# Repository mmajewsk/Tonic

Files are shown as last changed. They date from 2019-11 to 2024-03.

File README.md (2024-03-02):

<div align="center">
  
# An open-sourced project of autonomous car 
  
[Introduction](#introduction) • [Documentation](#ok-so-how-do-i-start) • [Screenshots] • [Contribute](#contribute) 
  
Tonic logo



[][Discord]

demo

⚠️ ➡️ [Video here](https://www.youtube.com/watch?v=u7oDqWJhXR0) ⬅️ ⚠️

_a.k.a.: "Roomba, that does not suck"_

Written in Python 🐍 (mostly).

</div>

---

### Contents:

- [Introduction](#introduction)
- [Features](#features) 
- [How does it work](#how-does-it-work) 
- [How to start](#ok-so-how-do-i-start)
- [Contribution](#contribute)
- [Related repos](#related-repos)

# Introduction

This repository contains main software and documentation for the Tonic project. This project aims to create an open-sourced autonomous driving system, along with its hardware prototype implementation. Some essential parts of the projects are contained in other related repos. See [the list of related repos](#related-repos)
The core idea of how this should work is as follows:

1. After setting up the robot/car, drive it manually, and dump the video and steering feed (this part is called _data taking_).
2. Create a 3D mapping of the environment with [Tonic/autonomous].
3. Define checkpoints, through which the machine will drive.
4. Program the car to drive on the defined paths.

All of that to be possible for as cheap as possible, with a raspberry PI and only a single camera.

# Features

  

  - Camera live feed and recording.
  - Live steering system and recording.
  - Working IMU live streaming and recording.
  - Working odometry live streaming and recording.
  - Qt GUI client for driving and data taking.
  - SLAM mapping, and navigation implemented with ORB_SLAM2 and its custom fork, custom python bindings, and serialisation.

# How does it work

As for now, this repository ([mmajewsk/Tonic]) contains guides and software for building, running and steering the car 🚘 for the _data taking_.
The code is divided, into [Tonic/control] and [Tonic/car]. 

The [Tonic/control] contains the code that is meant to be run on your laptop/pc/mac, that will control the raspberry pi [Tonic/car].

The machine and control interface is communicating via WiFi network, using sockets. 

Sensors, camera, and steering - each one is implemented as a separate service using sockets.
You can steer it with the keyboard on PC, while seeing live feed from the camera.
All of the sensors, steering and video can be dumped to files on PC.
You don't need to turn all of the sensors to make this work.

**The odometry and IMU are not necessary to make an environment mapping**

# Ok so how do I start

0. Take a look at previous versions and the current one in [video and screenshots][Screenshots].
1. First start by [assembling the hardware](doc/hardware_guide.md).
2. Then set up the [machine and interface software](doc/running_software.md).
3. Do the data-taking run, running steering and video data, [as described here](doc/running_software.md##running-tonic).

To make your machine drive autonomously, follow the guide in [Tonic/autonomous] repo.

# Contribute

🧑‍🔧 This project is meant to be open for everyone. The contributions are welcome.
If you would like to help see what's listed in the issues [here](https://github.com/mmajewsk/Tonic/issues), or add something yourself.

Also, you can join the 🗣️ [discord server][discord] if you are looking for quick help, or just want to say hi ;) 

# Related repos
- [My fork of ORB_SLAM2](https://github.com/mmajewsk/ORB_SLAM2)
- [My fork of Osmap] - Dumps ORB_SLAM2 to file
- [My fork of PythonBindings] - this one combines osmap with orb slam python bindings!
- [TonicSlamDunk] - Install scripts for all of the above, includes scripts for ubuntu, and dockerfile.
- ~~[TonicOrange] - **Exemplary use of orb slam, for pathfinding**~~ (moved to [Tonic/autonomous])

[discord]: https://discord.gg/shmRajSkDz
[mmajewsk/Tonic]: https://github.com/mmajewsk/Tonic
[Tonic/control]: control
[Tonic/car]: car
[My fork of ORB_SLAM2]: https://github.com/mmajewsk/ORB_SLAM2
[My fork of Osmap]: https://github.com/mmajewsk/osmap 
[My fork of PythonBindings]: https://github.com/mmajewsk/ORB_SLAM2-PythonBindings 
[TonicSlamDunk]: https://github.com/mmajewsk/TonicSlamDunk 
[TonicOrange]: https://github.com/mmajewsk/TonicOrange 
[Screenshots]: doc/video_and_screenshots.md
[Tonic/autonomous]: autonomous

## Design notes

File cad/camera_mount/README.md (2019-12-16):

# Description

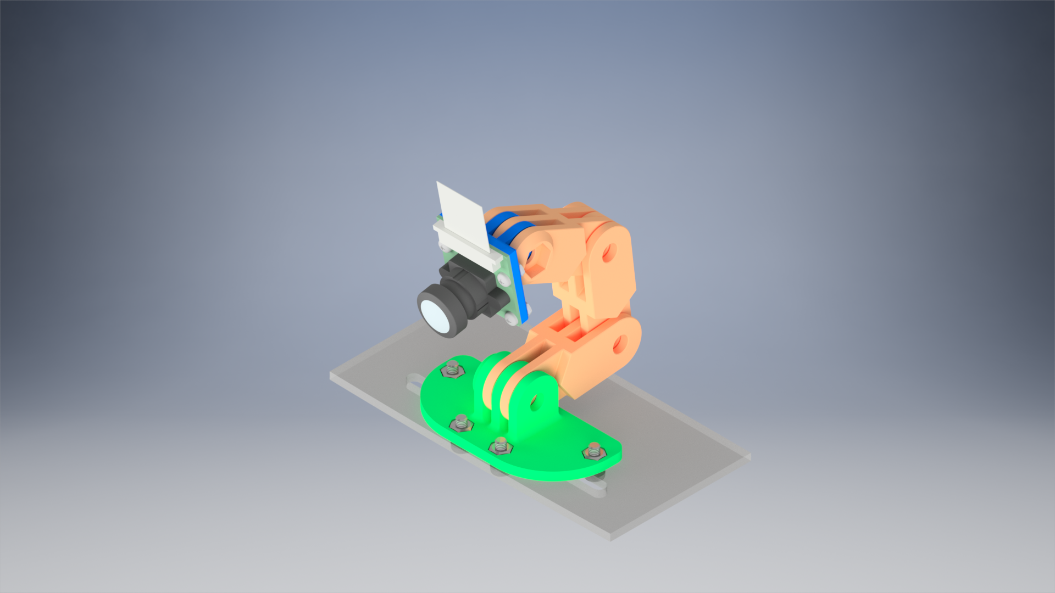
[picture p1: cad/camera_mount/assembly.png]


This Raspberry Pi camera mount makes use of the action cam style bracket connector (aka GoPro-inspired).
IMU mount suits [MinIMU-9 v5](https://www.pololu.com/product/2738).

arm-30-straight-v5-1.stl was borrowed from [https://www.thingiverse.com/thing:2194278](https://www.thingiverse.com/thing:2194278)

Made with Autodesk Inventor 2020

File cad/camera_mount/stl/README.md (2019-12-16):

# Print settings:

The higher infill density you pick the sturdier your parts are going to be.
Go for 100% if you can.

## camera_mount.stl

* Generate supports: yes

## camera_mount.stl

* Generate supports: no

## platform_mount.stl

* Generate supports: yes

## arm-30-straight-v5-1.stl

* Print 3 pieces
* Generate supports: no

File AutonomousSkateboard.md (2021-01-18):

# AutonomousSkateboard

This repository will contain notes on the autnomous skateboard.

# Motivation 

It's cheap. It can move a person around. Can be upgraded to auotonomy. What else do you need? 

# Simmilar work

Hacksmith did a remotely controlled board like that (timestamp points to specific) so I know it's possible, but they dida that with 4 motors.
https://www.youtube.com/watch?v=1g5nzRINaPQ&t=368s
Question is will 2 motors be enough to turn the board around?

# Hardware

If you are not familliar with DIY e-skateboards i suggest watching some videos on this topic [like this one  ](https://www.youtube.com/watch?v=LJqyWRSqOy4).

There are multiple parts availible online to buy and assemble, but the cheapest option is to recycle.
I bought [Nillox Longboard](https://www.nilox.com/es/datasheet/electric-skateboard-30nxskmolo001) for mere ~100€.
It was described as broken, but the description suggested tha the battery and wheels are ok, so I risked buying it.

The battery is 4,4 Ah 36V 10s2p with BMS (Battery Management System) built-in.
The motors are 90mm motors (kind of like [these](https://www.amazon.com/PROMOTOR-Motors-Electronic-Skateboard-Longboard/dp/B07F2Y22Q9?th=1)). I don'thave much details but will work this out.

The internal electronic was kind of fine (the problem with the board not working was only with the remote control itself), but still for better control I needed an ESC (electric speed control).

This is where the wonderful, glorious [VESC](https://vesc-project.com/) project comes in.
TL; DR; its highly customisable, open-source elecetric speed control.
I bought 2x flipsky's version of [VESC](https://flipsky.net/products/torque-esc-vesc-%C2%AE-bldc-electronic-speed-controller) (2x one per motor).

# Controlling the speed

The two VESCs can be connected together to duplicate the steering signal.
The VESC can be connected to mobile app or PC via bluetooth (using a proprietary [bluetooth module](https://flipsky.net/products/core51822-ble4-0-bluetooth-2-4g-wireless-module-nrf51822-onboard-ws82013)]. So that's a nice wireless connection.
The main problem is that VESC was not designed with differential steering (we need to move one wheel faster then the other to make it turn) in mind.
There are two possible sollutions:
 - Use external connection to controll VESCs with PWM (pulse-width modulation), so something like arduino would work
 - Dig into the VESC code to find if it's possible to send a different command to the connected vesc than just to repeat. And modify the code to do so.
 So far I'm opting for the second one since it should be more elegant and versatile, but the first one is far easier to implement, but needs additional hardware.

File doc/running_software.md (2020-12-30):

# Software Guide

So in order to make the robot work, you need to setup everything on raspberry ([car setup](#car-setup)) and on your pc ([remote control](#remote-control)).

## Steps to run in data taking mode

There is some set up required, before you can run this:

0. Set up the [RPI0](#car-setup)
1. (callibrate the IMU, but only if you need it)
2. Set up the `settings.yml` correctly
3. Set up desired services on the RPI0(Video, Steering, Imu, Odometry).
4. [Set up remote control](#remote-control-setup) and run it.

## (Deprecated) Steps to run in live orb_slam mode

There is some set up required, before you can run this:

0. Set up the [RPI0](#car-setup) and [SLAM docker](https://github.com/mmajewsk/orb_slam_py2_docker)
1. callibrate the camera
2. callibrate the IMU
3. Set up the `settings.yml` correctly
4. Set up desired services on the RPI0(Video, Steering, Imu, Odometry), or on laptop (SLAM).
5. Run Tonic 

# Remote Control

## Prerequisistes

**Python** - Of course, Tonic is written almost entirely in python, so you will be needing python 3.6 at least. I highly recommend using [Anaconda](https://www.anaconda.com/download/)

**OpenCV** - For some scripts it will be necessesary to use OpenCV. No way around it. 
If you are using anaconda you can simply do :

```
conda install -c menpo opencv
```
**Python Dependencies**

You are using python, so just do:

```
pip install -r requirements.txt
```

**Warning** I did not test different configrations, hit the issues in github if something is not working for you.

# Remote control setup

You need to follow these steps:

### 1. Seting up RPI0 and SLAM
For guide for setting up RPI0 look [here](#device-setup).
How to set up SLAM docker see [here](https://github.com/mmajewsk/orb_slam_py2_docker).

### 2. Configuring settings.yml

In the `pc` folder there is `settings.yml` file. Lets take a look:

```
info:
  settings: v1
  car:
    build: mark2
    name: car1
hardware:
  camera:
    calibration_file:
      path: camera_calibration/calib.json
      type: json
    image:
      shape: [320, 240, 3]
server:
  ip: '192.168.1.98'

  video:
    port: 2201
    command: "python -u video_streaming.py"
  steering:
    port: 2203
    command: "python3 -u steering_server.py"
  imu:
    port: 2204
    command: "python -u imu_server.py"
  odo:
    port: 2206
    command: "python3 -u odometry.py"
  slam:
    ip: '127.0.0.1'
    port: 2207
  master:
    port: 2205
```

We can divide it into three parts:

`info` - just some informations, not really important.

`hardware` - stores information about desired images shape as well as path to json containing calibration.

`server` - stores the configuration of services. the `ip` is the ip of the RPI0, fill it in accordingly.
Also fill in the `ip` in `slam`, if you are not running it on the same machine as Tonic.

### 3. Running Tonic

```
python run.py -v -s
```

This should run the Tonic with connected Video feed and active steering.
The steering (WASD keys only!) is only active when you have clicked into the window with the feed.
You can run Tonic with any number of options specified in the help menu.
Altough, **to run SLAM you have to run it with Imu** (`-i`).

To collect the all data from all sensors, you should run:

```
python run.py -s -v -i -o --dump_video --dump_steering --dump_imu --dump_odo /path/to/folder/to/dump/data/to
```

Each of the options is described in help `python run.py -h`.
**Remember to change the folder if you want to take new data, because it will defaultly overwrite existing data**

# Car Setup

This section will guide throug the usage of the `car` folder.
The code was used on Raspberry Pi Zero with WIFI.
It was not tested on any other device.

## How to use this

The recommended workflow is to open as many ssh connections from your machine to the RPI as needed and in each ssh run one of the services.
This is also why some of the requirements are mutually exclusive (python 2 and 3). But you should have both installed, and just run the separately.
Yes, this is not nice, but unifying everything so it would work as reliably is on the todo list ;)  

## Prerequistes

I am assuming that your car is already built. If not you can use [the hardware guide](#hardware_guide.md).
After you will set up the car, you need to be connect it to the same network as the device that you will be running Tonic on.
There is enough guides on how to connect the RPI to the wifi already so go and find one.
Remember to put the Raspberrys IP into the [settings](#2.-configuring-settings)

As stated previously you can skip the IMU and odometry steps, and use only steering and video.

**Video** - This service requires **Python 2** [picamera](https://picamera.readthedocs.io), but it should already be in your raspberry.
Remember to enable the camera in the RPI settings!

**Steering** - Nothing more than [RPI GPIO](https://pypi.org/project/RPi.GPIO/) and **python 3**

**Odometry** - Nothing more than [RPI GPIO](https://pypi.org/project/RPi.GPIO/) and **python 3**

**IMU** - The imu services uses external IMU driver, [minimu9-ahrs](https://github.com/DavidEGrayson/minimu9-ahrs) by DavidEGrayson. This one might be tough, but the guide on the drivers repo got me through anyway, be patient, make sure that you have nabled the correct settings, and everything is well soldered and connected. 
the guide is [here](https://github.com/DavidEGrayson/minimu9-ahrs#getting-started). Godspeed!

Internally this service opens `subprocess.Popen` to call miminu9-ahrs (yeah, i know, thats not the best solution, but I tried wrapping it in python and it took too much time).
**Make sure that minimu9-ahrs is working and is accesible for that script, and that it is callibrated!**

## Running

**Video**:

```
python video_streaming.py
```

And thats it.
If the connection is interupted, you might need to restart the service.

**Steering**

```
python3 steering_server.py
```

If your steering does not match with your hardware, you can easilly manipulate the code to get the desired output.
If the connection is interupted, you might need to restart the service.

**IMU**

```
python imu_server.py
```

Additionaly, if you will stop connection with the Tonic/pc, you dont need to reset this service.

**Odometry**

```
python3 odometry.py
```

## Unifying the service (not fully supported)

There was an attempt to unify every service, so it would not need 4 windows to be managed.
You can see the code in the file `master_server.py`.

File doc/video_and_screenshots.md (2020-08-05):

# The third version

![Third version, less spectacular](https://lh3.googleusercontent.com/IuCSr21Cb3tGpGMnIhsa7TThIg2WQow34TMnW2t3mI2jwENIGsg7YI2H-PUxN7tL1rPp5GF8OytFAX5TnJt4F91LoR5jvWLSZfbNOt-bqljZWx_-JIScLlvS8kxXzLI2Gl5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)

Third version was created because of the problems with the steering (cheap remote controled cars have low quality gears inside). 
Also, in the previous version, any manipulation of the circuits, was difficult because of the casing. 
Also it was difficult to get good odometry readout. 

So i changed the body of the car as well as the wheels. 
Looks a bit worse, but is waaaaay more effective ;]

# Old versions

second version (video) (https://www.youtube.com/watch?v=XM7lNRdp8ow)
    
  **Attention! This is cool!** ORB-slam working on the camera feed (video):
  
  Second version (video) (https://www.youtube.com/watch?v=XR-vKycwOm8)
  
  **C A R E F U L! This is cool as well** 2D map from the video feed (video):
  
  Second version (video) (https://www.youtube.com/watch?v=Wd5jEd4hx6U)
  
  **reconstruction of camera feed in meshroom**
  
  3D reconstruction (https://www.youtube.com/watch?v=oRmxJyJHEtU)

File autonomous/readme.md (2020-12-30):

# TonicAutonomous.



This repository contains a code for navigation and autonomous driving of the [Tonic](https://github.com/mmajewsk/Tonic) project.

## Step by step
So how to use this. This repository was written in extensibility in mind. Altough this guide gets you through the process, the repository was designed for you to use it however you like it, by using the code itself.

### Setup 
I'm assuming that you have built, installed and properly configured [Tonic](https://github.com/mmajewsk/Tonic).
Also, you will need to also install this dependencie using [absolutely unholy abomination of a script](https://github.com/mmajewsk/TonicSlamDunk) ``./install.sh` - should be ok on 16.04 and 18.04.
Or use a docker (also described in that repo) [mwmajewsk/tonic_slam_dunk](https://hub.docker.com/repository/docker/mwmajewsk/tonic_slam_dunk).

Then before you start messing around with this repo, you should drive your Tonic car around, and record the video data.

```
python run.py -v -s --dump_video ~/path/to/video/dump
```

After that, you can go to the Tonic/autonomous directory. Activate the conda environment that contains SlamDunk installation (or use docker).

### 1. Run a script that creates required rgb.txt file in the data dump
```
(SlamDunkEnv2) python scripts/make_rgbtxt.py ~/path/to/video/dump
```

### 2. Create a map using map\_creator.py

First try out the dataset:

```
(SlamDunkEnv2) python map_creator.py /path_to/vocabulary_file/slam_dunk/builds/data/ORBvoc.txt /path_to/camera_calibration/os2py_applied/TUM-MINE-wide.yaml /path/to/video/dump
```

There are some options that you can use, you can change beginning and end of the images used for the map.
You can use them in reverse, or even save and load the map.
You can read data from one set of pictures, save the map, then read it with other set of pictures, improving your map. The possibilities are limitless :D 
Use options of the script to your advantage. When you are satisfied with the setup, dump the map using `--save_map`.

### 3. Use generated map to set up checkpoints

Checkpoints are points on the map that you want your car to go through.
The easiest way to use them is to first filter the images to look for those that can be used as checkpoints.

```
(SlamDunkEnv2) python filter_checkpoints.py  ~/path/to/map_dump/assoc.json ~/path/to/video/dump ~/path/to/filtered/checkpoints_filtered
```

Now choose images of the places that you want your car to get to.
From this point you have two options.

Either you write the names of the images in a text file (the car will be navigated through them in the order they) like this:

```
frame00110_1604587599.312472.jpg
frame00145_1604587601.440924.jpg
frame00211_1604587605.4512722.jpg
```

Or you create additional folder `chosen_checkpoints/` and put selected images there.

### 4. Run main.py

As this is work still in progress, for now you have edit the code of `main.py` in order to point all of the necessary paths into the right places. 
You will have to run two processes simultaenously on the car itself (i recommend using tmux).

```
python video_streaming.py
```

```
python3 steering_motors.py
```

Then simply run `(SlamDunkEnv2) python main.py`

## Further reading

graph theory books
http://www.maths.lse.ac.uk/Personal/jozef/LTCC/Graph_Theory_Bondy_Murty.pdf
http://www.esi2.us.es/~mbilbao/pdffiles/DiestelGT.pdf

hypergraph
https://www.researchgate.net/publication/339228370_Hypergraphs_an_introduction_and_review

slam tutorial
http://www2.informatik.uni-freiburg.de/~stachnis/pdf/grisetti10titsmag.pdf

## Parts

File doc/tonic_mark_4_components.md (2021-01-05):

## Tonic MARK 4 - List of components

||================Component==========|Price estimation|
|---|---|---|
|Onboard computer|[Raspberry Pi Zero W](https://www.amazon.com/Raspberry-Pi-3-Computer-Board/dp/B07KKBCXLY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) | 40$
|Camera| [Pi Camera wide angle](https://www.amazon.com/kuman-Raspberry-Camera-Module-OV5647/dp/B06XKLLT6G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) | 17$
|Chassis|- something like this [chassis](https://www.amazon.com/d/Robotics-Kit/diymore-Chassis-Encoder-Battery-Arduino/B01LWYUQPH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) to mount everythin with a pair of wheels with motors| 23$
|Wheels and motors| These usually come with the chassis, but if not aim for something like [these popular wheels and motors](https://www.amazon.com/Stemedu-Gearbox-Motor-200RPM-Arduino/dp/B07L881GXZ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), this also can be purchased as kit with a chassis | if not included in chassis 10$
|Camera mount| [3D printed camera mount](cad/camera_mount) | (?$)
|motor driver| [L298N - Dual Drive control](https://www.amazon.com/Qunqi-Controller-Module-Stepper-Arduino/dp/B014KMHSW6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) | 7$ 
| camera connector|[sunny connector for camera](https://www.amazon.com/Arducam-1-0mm-Camera-Raspberry-Version/dp/B076Q595HJ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)| 8$
|power source| [Li-Pol 900mAh 20C 3S 11,1V](https://botland.com.pl/akumulatory-li-pol-3s-111v-/8320-pakiet-li-pol-redox-900mah-20c-3s-111v.html) - or any one matching specs| 13$
|other|for RPI0 [GPIO pins](https://www.amazon.com/DIKAVS-Break-Away-2x20-pin-Header-Raspberry/dp/B075VNBD3R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) you may find already in some raspberry pi zero sets| if not included 10$
|sum|---------------| 80$ |

### Optional
||================Component==========|Price estimation|
|---|---|---|
|IMU| Pololu MinIMU-9 v5 | It does not need to be a exact match, but you will have to modify the code to cover it - 20$
|Odometry|[photo interrupter](https://www.amazon.com/Waveshare-Photo-Interrupter-Sensor-Measuring/dp/B01N0FQ21B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)| 10$
|Batterry monitor|[this cheap thing](https://www.amazon.com/PACK-Battery-Voltage-Checker-Alarm/dp/B00XQ91ECA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)| $10
|current stabiliser|[1500uf 15v capacitor](https://www.amazon.com/pcs-Panasonic-FM-Capacitors-1500uf/dp/B073YQB53H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)| $2

### Things that you may already have or buy once
||================Component==========|Price estimation|
|---|---|---|
|charger|[Charger for battery](https://botland.com.pl/ladowarki-lipol-sieciowe/1240-ladowarka-redox-lipo-z-zasilaczem.html)| 14$
| cables | Pair of T-DEAN connectors| 2$
| cables | some [connecting cables](https://www.amazon.com/Elegoo-EL-CP-004-Multicolored-Breadboard-arduino/dp/B01EV70C78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)| 7$

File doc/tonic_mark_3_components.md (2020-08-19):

## Tonic MARK 3 - List of components

||================Component==========|Price estimation|
|---|---|---|
|Onboard computer|[Raspberry Pi Zero W](https://www.amazon.com/Raspberry-Pi-Zero-Wireless-model/dp/B06XFZC3BX) | 15$
|Camera| [Pi Camera](https://www.amazon.com/kuman-Raspberry-Camera-Module-OV5647/dp/B06XKLLT6G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) with connecting tape ~ 16$ - You need specifically this connecting tape for pi zero, as it is different than for other raspberry versions| 10$
|Chassis|- something like this [chassis](https://www.amazon.com/d/Robotics-Kit/diymore-Chassis-Encoder-Battery-Arduino/B01LWYUQPH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) to mount everythin with a pair of wheels with motors| 23$
|Wheels and motors| These usually come with the chassis, but if not aim for something like [these popular wheels and motors](https://www.amazon.com/Stemedu-Gearbox-Motor-200RPM-Arduino/dp/B07L881GXZ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), this also can be purchased as kit with a chassis | if not included in chassis 10$
|Camera mount|- [camera case](https://www.amazon.com/components-Latest-Raspberry-Camera-Megapixel/dp/B00IJZJKK4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) this camera case, or you can 3Dprint one.| 4$
|motor driver|- [L298N - Dual Drive control](https://www.amazon.com/Qunqi-Controller-Module-Stepper-Arduino/dp/B014KMHSW6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) | 7$ 
| camera connector|-  - [sunny connector for camera](https://www.amazon.com/Arducam-1-0mm-Camera-Raspberry-Version/dp/B076Q595HJ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)| 8$
|power source| [Li-Pol 900mAh 20C 3S 11,1V](https://botland.com.pl/akumulatory-li-pol-3s-111v-/8320-pakiet-li-pol-redox-900mah-20c-3s-111v.html) - or any one matching specs| 13$
|other|for RPI0 [GPIO pins](https://www.amazon.com/DIKAVS-Break-Away-2x20-pin-Header-Raspberry/dp/B075VNBD3R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) you may find already in some raspberry pi zero sets| if not included 10$
|sum|---------------| 80$ |

### Optional
||================Component==========|Price estimation|
|---|---|---|
|IMU| Pololu MinIMU-9 v5 | It does not need to be a exact match, but you will have to modify the code to cover it - 20$
|Odometry|[photo interrupter](https://www.amazon.com/Waveshare-Photo-Interrupter-Sensor-Measuring/dp/B01N0FQ21B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)| 10$
|Batterry monitor|[this cheap thing](https://www.amazon.com/PACK-Battery-Voltage-Checker-Alarm/dp/B00XQ91ECA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)| $10
|current stabiliser|[1500uf 15v capacitor](https://www.amazon.com/PACK-Battery-Voltage-Checker-Alarm/dp/B00XQ91ECA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)| $5

### Things that you may already have or buy once
||================Component==========|Price estimation|
|---|---|---|
|charger|[Charger for battery](https://botland.com.pl/ladowarki-lipol-sieciowe/1240-ladowarka-redox-lipo-z-zasilaczem.html)| 14$
| cables | Pair of T-DEAN connectors| 2$
| cables | some [connecting cables](https://www.amazon.com/Elegoo-EL-CP-004-Multicolored-Breadboard-arduino/dp/B01EV70C78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)| 7$

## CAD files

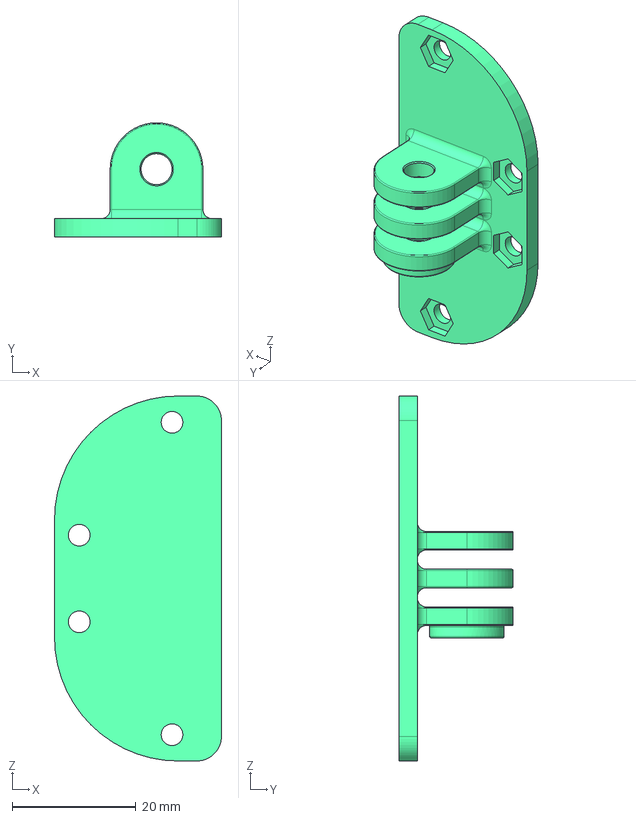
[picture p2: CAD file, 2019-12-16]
cad/camera_mount/step/platform_mount.stp
27.0 x 18.5 x 59.0 mm

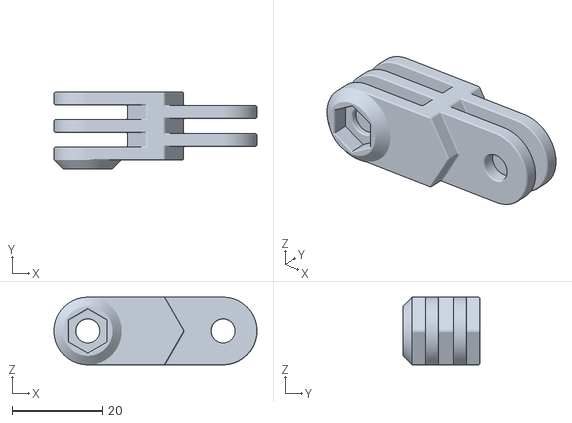
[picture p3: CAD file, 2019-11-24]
cad/camera_mount/stl/arm-30-straight-v5-1.stl
45.0 x 17.0 x 15.0

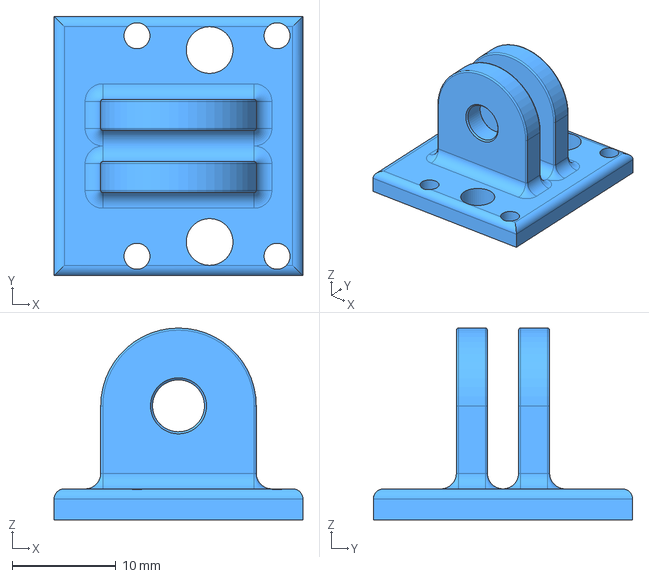
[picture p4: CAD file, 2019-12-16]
cad/camera_mount/step/camera_mount.stp
24.0 x 25.0 x 18.5 mm

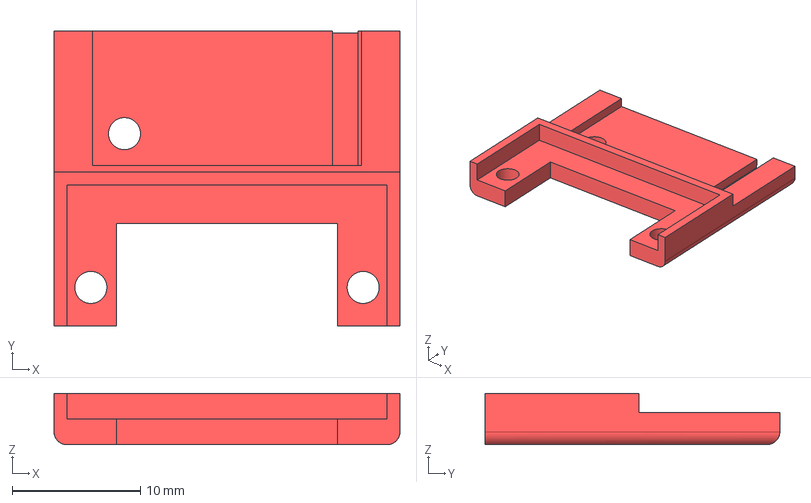
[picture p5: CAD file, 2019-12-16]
cad/camera_mount/step/imu_mount.stp
27.0 x 23.0 x 4.00 mm

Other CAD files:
cad/camera_mount/assembly.iam
cad/camera_mount/assembly_imu.iam
cad/camera_mount/platform_parts/camera/Raspberry Pi Camera (G) 160 deg.iam
cad/camera_mount/platform_parts/minimu-9.ipt
cad/camera_mount/platform_parts/platform.ipt
cad/camera_mount/printable/arm-30-straight-v5-1.ipt
cad/camera_mount/printable/camera_mount.ipt
cad/camera_mount/printable/imu_mount.ipt
cad/camera_mount/printable/platform_mount.ipt
cad/camera_mount/stl/camera_mount.stl
cad/camera_mount/stl/imu_mount.stl
cad/camera_mount/stl/platform_mount.stl

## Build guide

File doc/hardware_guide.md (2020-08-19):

# Hardware Guide

## Before you start

current_version

Remember that all you really need for this to work is steering and camera, and the IMU and odomoetry are optional. 
This entire hardware guide is __just a guide__. 

It is also a little bit outdated. The picture above presents the [Mark-4] version of the build, but the guide was created with [Mark-3].
This guid is still valid.

 - Since it was created I have changed the version of the raspberry PI to A+
 - And also changed the orientation of the camera (now the two wheels are front, and single one is on the back, as per this picture)
 - Thanks to [panovv](https://github.com/panovvv) the camera is now mounted with a [3D printed mount](https://github.com/mmajewsk/Tonic/issues/19), cad files of which you can find in the repository.
 
Feel free to modify your build.
If you can please reach me and send me pictures of your build, or your version of the guide ;)

## Lists of components, and versions

I have listed two versions of the components: 

- [Mark-3]
- [Mark-4]

This hardware guide was created with pictures from Mark-3, but is valid also for Mark-4 (except the camera mount).
The main difference between Mark-3 and Mark-4 is that Mark-4 uses Raspberry PI A+, and wide angle camera.
This change helped with stability of the process of data taking and mapping, but is slightly more expensive (+30$).
Either way, if you plan on using this project a lot, I highly recommend buying spare parts, as things can sometimes just stop working.
Especially the camera connectors, they keep dying on monthly basis :/ .

**Warning** You will be working with Li-Po batterries, please be safe and careful. Ideally read first this very nice post that explains how they work https://rogershobbycenter.com/lipoguide

## How to build this

### First assmble the chassis 
This should be pretty intuitive. But you can check out [this video](https://www.youtube.com/watch?v=H78t6dnSoG0).

### Mount raspberry

I used ot glue and zip-tie. Remember to orient it correct way, and leave the video connector accessible.

### Next mount the camera
Mount Imu as well. Ideally youwant it as close to the camera as possible.
I used some bolts and nuts to mount over front wheel.

camera-mount-image

## Mount the battery and on switch
Attach the battery under the chassis. I used a cable tie around PI and created a loop underneath chassis.

battery-mount

### Mount the drive control and RPI0

I used hot glue. Do not let cables touch the radiatior. Make it as stable as possible.

## Connecting the wires

For the reference to the RPI0 pinout, use [this](https://pinout.xyz/) website. I will use both the board numbering and BCM.
So here is the wiring scheme (**ITS NOT CORRECT - SEE ISSUE [#18](https://github.com/mmajewsk/Tonic/issues/18)** ):

wiring-scheme-bb
overall_wires

Some components may not match their real counterparts. Don't worry, I will guide through each component.

### PI0 to Camera

This is easy; just lift the plugs a little bit both at camera and PI.
The one on the raspberry is **very ease to break** so be careful, but dont feel bad if you accidentaly will break it. It just happens ;) 

camera-wiring

### PI0 to L298N
This one is is the trickiest.

Steering pins:

Pin 	|Raspberry BCM 	| L298N
------|---------------|--------
37 	  | BCM 26 	      | ENA
35 	  | BCM 19 	      | IN1
33 	  | BCM 13 	      | IN2
31 	  | BCM 6 	      | IN3
29 	  | BCM 29 	      | IN4
27 	  | BCM 0 	      | ENB

Power:

Pin 	|Raspberry BCM 	| L298N
------|---------------|--------
2 	  | 5v Power 	    | +5V
6 	  | Ground 	      | GND

wiring-driver-pins

The colors used on the wiring scheme are coresponding with photos.

### PI0 to encoders

Wiring of the pins and ground are as follow:

Pin 	|Raspberry BCM 	| Encoder
------|---------------|-----------
36 	  | BCM 16 	      | Right Encoder OUT
34 	  | Ground 	      | GND
32 	  | BCM 12 	      | Left Encoder OUT
30 	  | Ground 	      | GND

encoders-wiring

When it comes to voltage, I just split the cable coming from Pin 4 (5v Power) of RPI0

encoders-power-split

### PI0 to IMU

Be sure **not to mix those up**. They are a bit confusing. 

Pin 	|Raspberry BCM 	| IMU
------|---------------|---------
1 	  | 3v3 Power 	  | VDD
3 	  | BCM 2 	      | SDA
5 	  | BCM 3 	      | SCL
9 	  | Ground 	      | GND

IMU-wiring

### L298N to motors

Just connect OUT1 and OUT2 to the right motor, and OUT3 and OUT4 to the left.
If steering does not work properly, try switching cables in the motor.

### L298 to Power

Use power switch on one of the cables. Make sure that they cannot touch anything else.
**If you close the circuit on the battery it might blow up**
I also used t-dean connectors, and unplug it when im transporting the robot.

### L298 to capacitor

Im using 1500 micro-farad 16V capacitor. **Its polarised so make sure to properly orient it, and to put the minus into the ground**
It acts as a stabiliser, its not necessary but greatly improves the stability of the circuit.

[Mark-3]: tonic_mark_3_components.md
[Mark-4]: tonic_mark_4_components.md

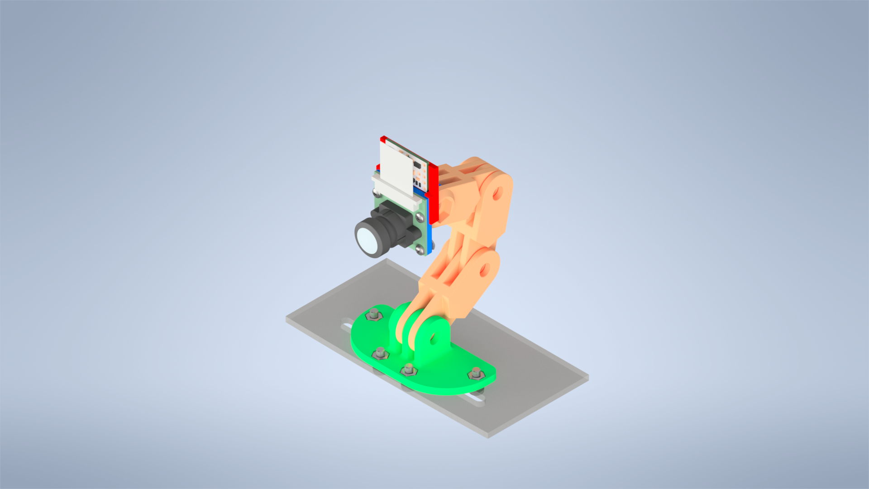
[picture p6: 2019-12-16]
cad/camera_mount/assembly_imu.png

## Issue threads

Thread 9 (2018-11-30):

New 3D printed mount for the camera

mmajewsk, 2018-11-30:
This is actually undergoing, I'm trying to modify this project https://www.thingiverse.com/thing:1579789

mmajewsk, 2020-12-30:
closed by https://github.com/mmajewsk/Tonic/pull/20

Closed 2020-12-30.

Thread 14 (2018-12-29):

Imu is sometimes stuck, add process watcher

mmajewsk, 2018-12-29:

mmajewsk, 2019-01-18:
This error happened
`Error: Failed to read from I2C: Remote I/O error (system:121)`

mmajewsk, 2019-01-19:
This 0ff8172e8fa229c42283a44cc20f77d5e2444b35 probably fixes the problem, tests are needed

Closed 2019-08-05.

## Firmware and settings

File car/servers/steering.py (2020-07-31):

from abc import ABCMeta, abstractmethod
import RPi.GPIO as GPIO
import time
import multiprocessing
import functools

class Steering(metaclass=ABCMeta):

	@abstractmethod
	def wheel_right(self, val):
		pass


	@abstractmethod
	def wheel_left(self, val):
		pass

	@abstractmethod
	def wheel_straight(self, val):
		pass

	@abstractmethod
	def stop_car(self, val):
		pass

	@abstractmethod
	def forward(self, val):
		pass

	@abstractmethod
	def backward(self, val):
		pass

class Motor:
	"""
	This class conttains logic for GPIO motor.
	"""
	def __init__(self, enabler_pin, plus_pin, minus_pin, velocity=0, high=100, frequency=100):
		self.enabler_pin = enabler_pin
		self.default_velocity = velocity
		self.minus_pin = minus_pin
		self.plus_pin = plus_pin
		GPIO.setup(enabler_pin, GPIO.OUT)
		GPIO.setup(minus_pin, GPIO.OUT)
		GPIO.setup(plus_pin, GPIO.OUT)
		self.enabler = GPIO.PWM(enabler_pin, frequency)
		self.LOW = 0
		self.HIGH = high
		self.enabler.start(0)
		self.last_val=0


	def set_values(self, val, p_val, m_val):
		val = val if val is not None else self.default_velocity
		print(val)
		self.enabler.ChangeDutyCycle(val)
		GPIO.output(self.plus_pin,p_val)
		GPIO.output(self.minus_pin, m_val)

	def __del__(self):
		self.enabler.stop()

class MotorDriver:
	def __init__(self, **kwargs):
		GPIO.setmode(GPIO.BCM)
		self.motor_a = Motor(enabler_pin=0, plus_pin=5, minus_pin=6, **kwargs)
		self.motor_b = Motor(enabler_pin=26, plus_pin=19, minus_pin=13, **kwargs)
		self.old_signal = None
		self.time_delay = 0.2

	def go(self, steering_dict):
		if self.old_signal is not None or self.old_signal!=steering_dict:
			self.motor_a.set_values(steering_dict['left'], self.motor_a.HIGH, self.motor_a.LOW)
			self.motor_b.set_values(steering_dict['right'], self.motor_b.HIGH, self.motor_b.LOW)
			self.old_signal = steering_dict
		time.sleep(self.time_delay)

	def __del__(self):
		GPIO.cleanup()

class SteeringDriverRobot(Steering):
	"""
	This class implements the functions of the movement for the car.
	You can create a new one like this so it would cover your configuration.
	"""
	def __init__(self, **kwargs):
		GPIO.setmode(GPIO.BCM)
		self.motor_a = Motor(enabler_pin=0, plus_pin=5, minus_pin=6, **kwargs['left_motor'])
		self.motor_b = Motor(enabler_pin=26, plus_pin=19, minus_pin=13, **kwargs['right_motor'])

	def wheel_right(self, val=None):
		pass

	def wheel_left(self, val=None):
		pass

	def forward(self, val=None):
		self.motor_a.set_values(val, self.motor_a.HIGH, self.motor_a.LOW)
		self.motor_b.set_values(val, self.motor_b.HIGH, self.motor_b.LOW)

	def backward(self, val=None):
		self.motor_a.set_values(val, self.motor_a.LOW, self.motor_a.HIGH)
		self.motor_b.set_values(val, self.motor_b.LOW, self.motor_b.HIGH)

	def stop_car(self, val=None):
		self.motor_a.set_values(0, self.motor_a.HIGH, self.motor_a.HIGH)
		self.motor_b.set_values(0, self.motor_b.HIGH, self.motor_b.HIGH)

	def wheel_straight(self, val=None):
		pass

	def forward_left(self, val=None):
		self.motor_a.set_values(10, self.motor_a.HIGH, self.motor_a.LOW)
		self.motor_b.set_values(val, self.motor_b.HIGH, self.motor_b.LOW)

	def backward_left(self, val=None):
		self.motor_a.set_values(10, self.motor_a.LOW, self.motor_a.HIGH)
		self.motor_b.set_values(val, self.motor_b.LOW, self.motor_b.HIGH)

	def forward_right(self, val=None):
		self.motor_a.set_values(val, self.motor_a.HIGH, self.motor_a.LOW)
		self.motor_b.set_values(10, self.motor_b.HIGH, self.motor_b.LOW)

	def backward_right(self, val=None):
		self.motor_a.set_values(val, self.motor_a.LOW, self.motor_a.HIGH)
		self.motor_b.set_values(10, self.motor_b.LOW, self.motor_b.HIGH)
	def __del__(self):
		GPIO.cleanup()


class SteeringDriverCar(Steering):
	def __init__(self, **kwargs):
		GPIO.setmode(GPIO.BCM)
		self.motor_a = Motor(enabler_pin=22, plus_pin=17, minus_pin=27, **kwargs['thrust'])
		self.motor_b = Motor(enabler_pin=24, plus_pin=4, minus_pin=23, **kwargs['steer'])

	def wheel_right(self, val=None):
		self.motor_b.set_values(val, self.motor_b.LOW, self.motor_b.HIGH)

	def wheel_left(self, val=None):
		self.motor_b.set_values(val, self.motor_b.HIGH, self.motor_b.LOW)

	def forward(self, val=None):
		self.motor_a.set_values(val, self.motor_a.HIGH, self.motor_a.LOW)

	def backward(self, val=None):
		self.motor_a.set_values(val, self.motor_a.LOW, self.motor_a.HIGH)

	def stop_car(self, val=None):
		self.motor_a.set_values(30, self.motor_a.HIGH, self.motor_a.HIGH)

	def wheel_straight(self, val=None):
		self.motor_b.set_values(val, self.motor_b.LOW, self.motor_b.LOW)

	def __del__(self):
		GPIO.cleanup()


class SteeringTranslator(Steering):
	def __init__(self, time_delay=0.4, **kwargs):
		self.time_delay = time_delay
		self.translator={
			'go_straight':[self.wheel_straight,self.forward],
			'go_backward':[self.wheel_straight,self.backward],
			'stop':[self.wheel_straight,self.stop_car],
			'forward_left':[self.forward, self.wheel_left],
			'forward_right': [self.forward, self.wheel_right],
			'backward_left': [self.backward, self.wheel_left],
			'backward_right': [self.backward, self.wheel_right],
			'left': [self.wheel_left],
			'right': [self.wheel_right],
		}
		self.command = ''
		self.old_signal = 'stop'

	def work(self, new_signal):
		if self.old_signal != new_signal:
			for f in self.translator[new_signal]:
				f()
			self.old_signal=new_signal
		time.sleep(self.time_delay)


	def run(self):
		signal = self.command_to_signal(self.command)
		print(signal)
		self.work(signal)


	def command_to_signal(self, command):
		if command.isspace() or not command:
			return 'stop'
		else:
			if 'w' in command and 'a' in command:
				return 'forward_left'
			elif 'w' in command and 'd' in command:
				return 'forward_right'
			elif 's' in command and 'a' in command:
				return 'backward_left'
			elif 's' in command and 'd' in command:
				return 'backward_right'
			elif 'd' in command:
				return 'right'
			elif 'a' in command:
				return 'left'
			elif 'w' in command:
				return 'go_straight'
			elif 's' in command:
				return 'go_backward'
			else:
				return 'stop'

class SteeringTranslatorCar(SteeringTranslator, SteeringDriverCar):
	def __init__(self, **kwargs):
		SteeringDriverCar.__init__(self, **kwargs)
		SteeringTranslator.__init__(self, **kwargs)

class SteeringTranslatorRobot(SteeringTranslator, SteeringDriverRobot):
	"""
	This class translates the commands to the functions of steering.
	"""
	def __init__(self, **kwargs):
		SteeringDriverRobot.__init__(self, **kwargs)
		SteeringTranslator.__init__(self, **kwargs)
		self.translator['go_straight'] = [self.forward]
		self.translator['go_backward'] = [self.backward]
		self.translator['stop'] = [self.stop_car]
		self.translator['forward_left'] = [self.forward_left]
		self.translator['forward_right'] = [self.forward_right]
		self.translator['backward_left'] = [self.backward_left]
		self.translator['backward_right'] = [self.backward_right]


def keys_to_command(keys):
		w,s,a,d = 87,83,68,65
		keytab = map(lambda x: keys[x], (w,s,a,d))
		command = sum(1<<i for i, b in enumerate(keytab) if b)
		return command

if __name__=='__main__':
	GPIO.setmode(GPIO.BCM)
	left_motor = dict(velocity=20, frequency=50, high=100)
	right_motor = dict(velocity=20, frequency=50, high=100)
	s = SteeringTranslatorRobot(left_motor=left_motor, right_motor=right_motor, time_delay=0.05)
	#s.signal = 'w'
	#s.run()
	s.stop_car()
	s.forward()
	time.sleep(0.2)
	s.stop_car()
	time.sleep(1)

	s.stop_car()
	s.forward()
	time.sleep(0.2)
	s.stop_car()
	time.sleep(1)

	s.stop_car()
	s.backward()
	time.sleep(0.2)
	s.stop_car()
	time.sleep(1)


	s.stop_car()
	s.forward_left()
	time.sleep(0.2)
	s.stop_car()
	time.sleep(1)

	s.stop_car()
	s.backward_left()
	time.sleep(0.2)
	s.stop_car()
	time.sleep(1)

	s.stop_car()
	s.forward_right()
	time.sleep(0.2)
	s.stop_car()
	time.sleep(1)

	s.stop_car()
	s.backward_right()
	time.sleep(0.2)
	s.stop_car()
	time.sleep(1)

	s.signal = ''
	#s.run()
	del s
	time.sleep(0.4)

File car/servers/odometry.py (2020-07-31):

import json
import multiprocessing
import RPi.GPIO as GPIO
import time
import datetime
from server_management import BaseServer, BaseClientHandler, ProcessLink
import logging
import asyncore
from abc import import ABC, abstractmethod


class OdometerBase(ABC):
	"""
	This class only purpose is to contain "history" property.
	"""

	@property
	@abstractmethod
	def history(self):
		"""
		This function should reset the history before returning the data (the return data should not repeat)
		Returns:
			List of tuples of (state, str(datetime.now())
		"""
		pass

class OdoSystemBase(ABC):
	"""

	"""
	@property
	@abstractmethod
	def data(self):
		"""
		Returns:
			Dict of history from OdometerBase
		"""
		pass


class Odometer(OdometerBase):
	def __init__(self, input_pin):
		self.input_pin = input_pin
		GPIO.setup(input_pin, GPIO.IN)
		self.prevous_state = self.status
		self._history = []

	@property
	def status(self):
		return GPIO.input(self.input_pin)

	def	check_slope(self):
		status = self.status
		if self.prevous_state != status:
			self._history.append((status, str(datetime.datetime.now())))
			self.prevous_state = status

	@property
	def history(self):
		tmp = list(self._history)
		self._history = []
		return tmp

class OdoSystem(multiprocessing.Process, OdometerSystemBase):
	def __init__(self, left_pin, right_pin, input_queue, output_queue, dt=0.05):
		multiprocessing.Process.__init__(self)
		self.dt=dt
		self.runnable = True
		self.input_queue=input_queue
		self.output_queue=output_queue
		GPIO.setmode(GPIO.BCM)
		self.left = Odometer(left_pin)
		self.right = Odometer(right_pin)
		self._data = {}

	def update(self):
		self.left.check_slope()
		self.right.check_slope()

	def process_command(self):
		while not self.input_queue.empty():
			command = self.input_queue.get()
			if command == "kill":
				self.runnable=False
			elif command == "read":
				self.output_queue.put(self.data)
	@property
	def data(self):
		return dict(left=self.left.history, right=self.right.history)

	def run(self):
		while self.runnable:
			for i in range(10):
				time.sleep(self.dt)
				self.update()
			self.process_command()


class OdoLink(ProcessLink):

	def __init__(self, left_pin, right_pin, dt):
		self.left_pin=left_pin
		self.right_pin=right_pin
		self.dt=dt
		ProcessLink.__init__(self)

	def create_process(self):
		return OdoSystem(self.left_pin, self.right_pin, self.input_queue, self.output_queue, dt=self.dt)

	def start(self):
		self.process.start()

	def read(self):
		self.input_queue.put("read")
		readout = dict(left=[],right=[])
		while not self.output_queue.empty():
			readout = self.output_queue.get()
		return readout


	def stop(self):
		self.input_queue.put("kill")

	def __del__(self):
		self.stop()
		ProcessLink.__del__(self)


class OdoClientHandler(BaseClientHandler):
	def __init__(self, sock, address, odo, jsonify=True):
		BaseClientHandler.__init__(self, sock, address, jsonify=jsonify)
		self.odo=odo

	def readout(self, input_data):
		return self.odo.read()


class OdoServer(BaseServer):
	def __init__(self,pins, address, dt=0.05):
		BaseServer.__init__(self, address)
		self.odo = OdoLink(pins[0], pins[1], dt)
		self.odo.start()
		time.sleep(5)

	def create_client(self, *args, **kwargs):
		return OdoClientHandler(*args, odo=self.odo, **kwargs)

def main():
	logging.basicConfig(level=logging.DEBUG, format='%(name)s:[%(levelname)s]: %(message)s')
	HOST = ''
	PORT = 2206
	s = OdoServer((12,16), (HOST, PORT), dt=0.01)
	asyncore.loop()


if __name__ == '__main__':
	main()

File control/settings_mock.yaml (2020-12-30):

info:
  settings: v2
  car:
    build: mark4
    name: car1
hardware:
  camera:
    calibration_file:
      path: camera_calibration/calib.json
      type: json
    image:
      shape: [320, 240, 3]
server:
  ip: '127.0.0.1'
  #ip: '192.168.1.133'

  video:
    port: 2201
  steering:
    port: 2203
  imu:
    port: 2204
  odo:
    port: 2206

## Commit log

2017-02-08 working steering and viewing on pc
2017-02-08 arduino steering complete
2017-04-25 deleting arduino folder
2017-05-23 implement deleting single frames from data_viewer
2017-05-31 added imu client and some client refactor
2017-06-01 more imu
2017-06-02 add basic imu window
2017-06-22 added basic map showup, modified the imu server (callibration)
2017-07-04 added new imu calibration car-side
2018-04-12 add service manager script and odometry
2018-12-15 finished wiring text
2018-12-18 Hardware guide (#12)
    * created basic hardware guide #10
    * added more info to hardware guide
    * finished wiring text
    * fixed tables
    * added photos, fixed tables
    * Update hardware_guide.md
2018-12-23 added device setup guide
2018-12-23 merging device setup with README
2019-01-18 improve imu and fix stuck bug
    [imu_interceptor.py, imu_server.py, imu_server_2.py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]
2019-01-19 some cleanup in imu processing
2019-10-10 camera mount
    [arm-30-straight-v5-1.ipt, arm-30-straight-v5-1.stl, assembly.iam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]
2019-12-11 imu mount
    unignore parts folder, add STEP files for platform agnosticism
    [Raspberry Pi Camera (G) 160 deg.iam, arm-30-straight-v5-1.ipt, assembly.iam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]
